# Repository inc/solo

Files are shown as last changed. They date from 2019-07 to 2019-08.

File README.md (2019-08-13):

# SOLO IOT motor controller

## Overview

SOLO is an IOT motor controller board designed by Lone Dynamics.

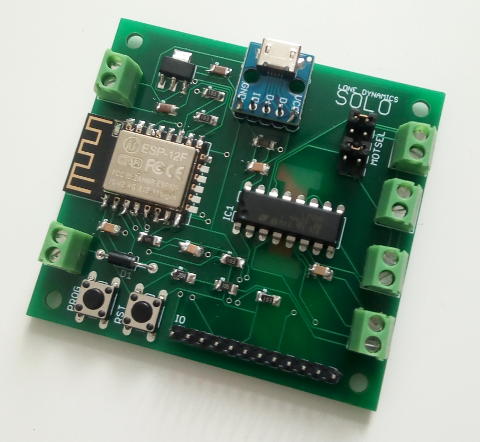
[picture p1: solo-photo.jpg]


## Features

  * Supports ESPEasy to provide a web-based interface and MQTT support over WiFi
  * Controls 2 (bidirectional) or 4 (unidirectional) DC motors
  * Power via MicroUSB or batteries and a solar panel
  * Battery voltage monitoring
  * Hand-solderable with a soldering iron

## Specifications

| | |
| --- | --- |
| Dimensions | 65mm x 60mm |
| WiFi Module | ESP-12E or F |
| Motor Controller | L293D |
| Power | MicroUSB, 4xAA NiMH batteries, 6V solar panel |

## Header Pinout

| Pin | Function |
| --- | --- |
| 1 | VCCBAT |
| 2 | VCC3V3 |
| 3 | ESPTXD |
| 4 | ESPRXD |
| 5 | ESPRST |
| 6 | GND |
| 7 | MOTOR12EN |
| 8 | MOTOR34EN |
| 9 | MOTOR1A |
| 10 | MOTOR2A |
| 11 | MOTOR3A |
| 12 | MOTOR4A |

## Board

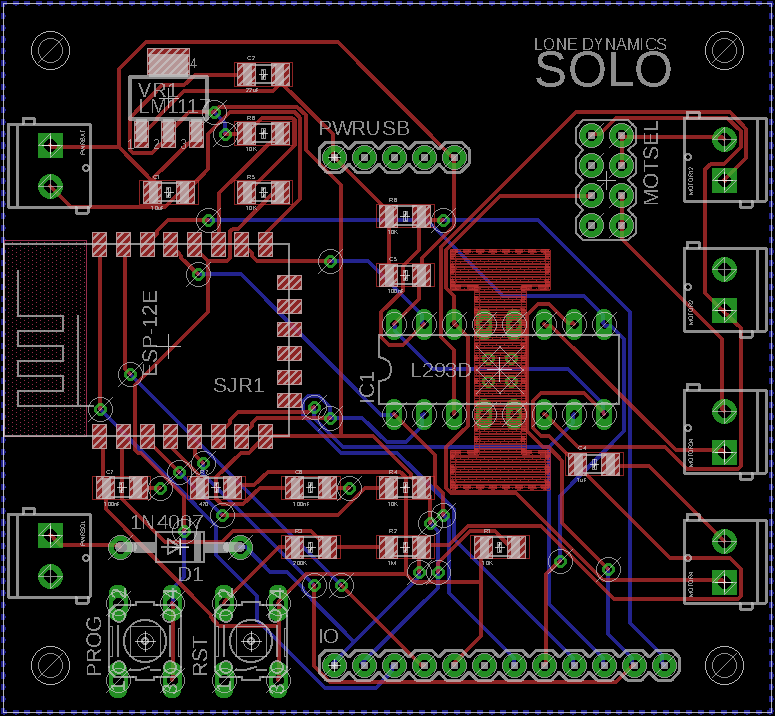
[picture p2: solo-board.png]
Board


## Schematics

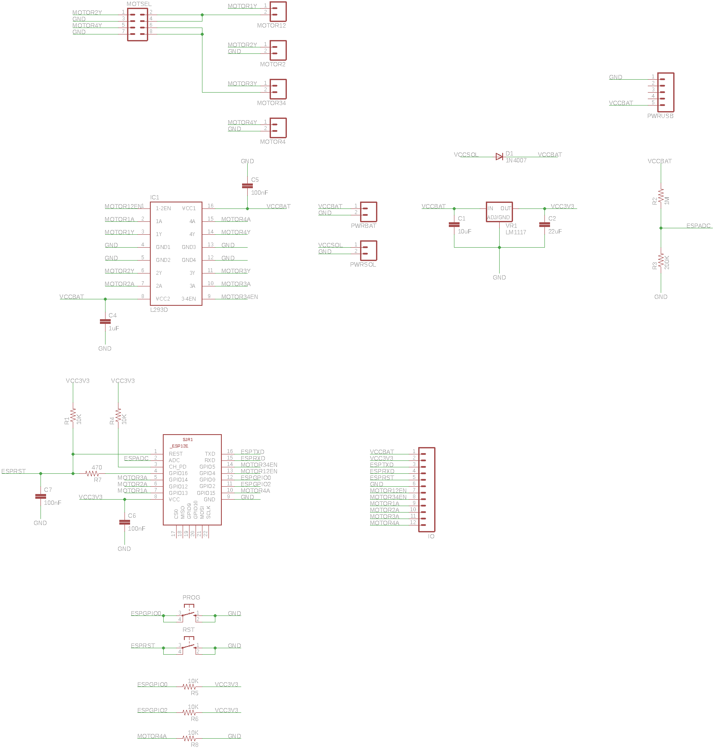
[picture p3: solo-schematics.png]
Schematics


## Known Issues (revision 0)

  * Pull-down resistors (10K) should be added to MOTOR12EN and MOTOR34EN to prevent the L293D from being enabled while the ESP is in sleep mode
  * Heatsink cutout doesn't expose copper
  * Has no built-in battery over-voltage protection

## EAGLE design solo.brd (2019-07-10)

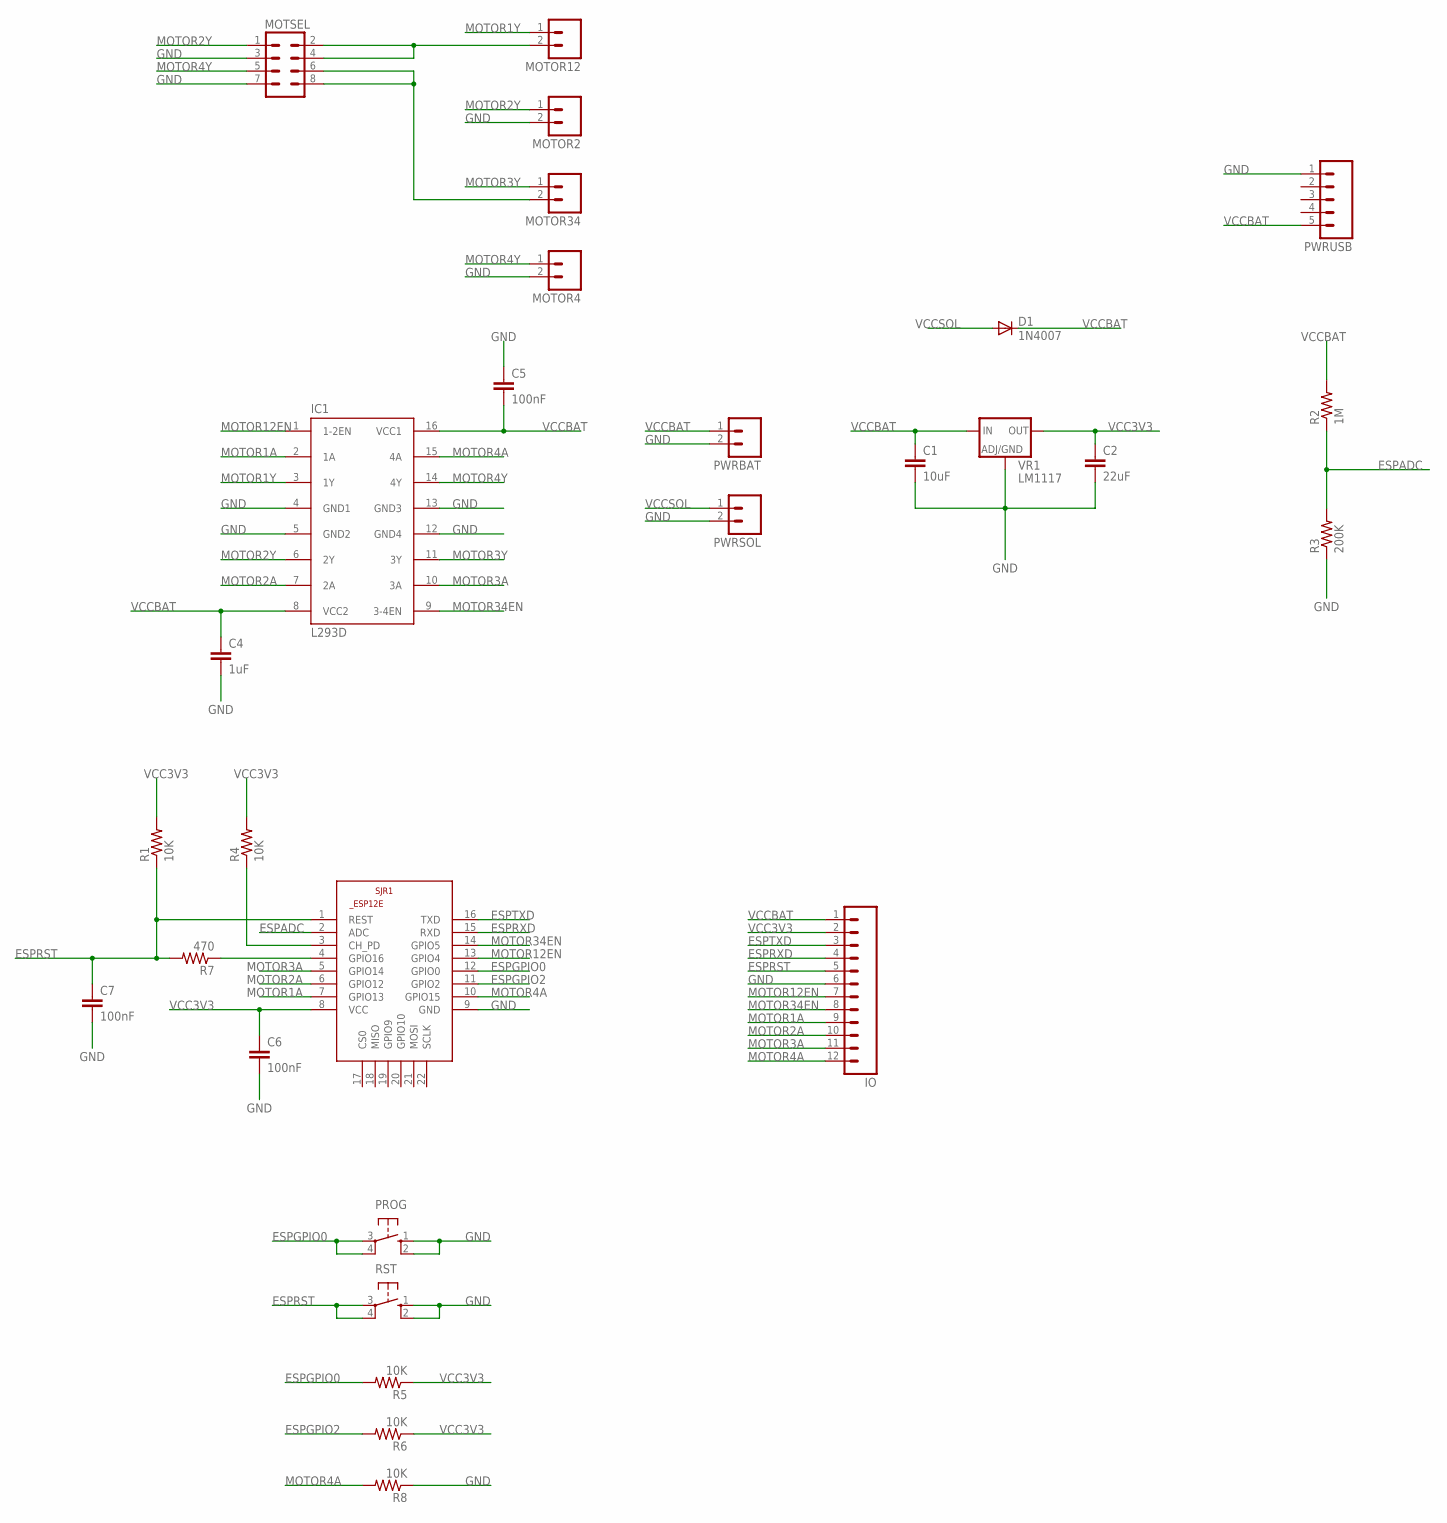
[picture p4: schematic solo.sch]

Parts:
C1: 10uF; 1206
C2: 22uF; 1206
C4: 1uF; 1206
C5, C6, C7: 100nF; 1206
D1: 1N4007; DO41-10
IC1: L293D; DIL16
IO: M12PTH; 1X12
MOTOR2, MOTOR4, MOTOR12, MOTOR34: M023.5MM; SCREWTERMINAL-3.5MM-2
MOTSEL: M04X2; 2X4
PROG: 10-XX; B3F-10XX
PWRBAT: M023.5MM; SCREWTERMINAL-3.5MM-2
PWRSOL: M023.5MM; SCREWTERMINAL-3.5MM-2
PWRUSB: M05PTH; 1X05
R1, R4, R5, R6, R8: 10K; 1206
R2: 1M; 1206
R3: 200K; 1206
R7: 470; 1206
RST: 10-XX; B3F-10XX
SJR1: ESP8266-12EESP12E; ESP8266-ESP12E
VR1: LM1117; SOT223

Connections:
ESPADC: R2.1, R3.2, SJR1.2 (ADC)
ESPCHPD: R4.1, SJR1.3 (CH_PD)
ESPGPIO0: PROG.3, PROG.4 (P1), R5.2, SJR1.12 (GPIO0)
ESPGPIO2: R6.2, SJR1.11 (GPIO2)
ESPRST: C7.1, IO.5, R1.1, R7.2, RST.3, RST.4 (P1), SJR1.1 (REST)
ESPRXD: IO.4, SJR1.15 (RXD)
ESPTXD: IO.3, SJR1.16 (TXD)
GND: C1.2, C2.2, C4.2, C5.1, C6.2, C7.2, IC1.4 (GND1), IC1.5 (GND2), IC1.12 (GND4), IC1.13 (GND3), IO.6, MOTOR2.2, MOTOR4.2, MOTSEL.3, MOTSEL.7, PROG.1 (S), PROG.2 (S1), PWRBAT.2, PWRSOL.2, PWRUSB.1, R3.1, R8.1, RST.1 (S), RST.2 (S1), SJR1.9 (GND), VR1.1 (ADJ/GND)
MOTOR1A: IC1.2 (1A), IO.9, SJR1.7 (GPIO13)
MOTOR1Y: IC1.3 (1Y), MOTOR12.1
MOTOR2A: IC1.7 (2A), IO.10, SJR1.6 (GPIO12)
MOTOR2Y: IC1.6 (2Y), MOTOR2.1, MOTSEL.1
MOTOR3A: IC1.10 (3A), IO.11, SJR1.5 (GPIO14)
MOTOR3Y: IC1.11 (3Y), MOTOR34.1
MOTOR4A: IC1.15 (4A), IO.12, R8.2, SJR1.10 (GPIO15)
MOTOR4Y: IC1.14 (4Y), MOTOR4.1, MOTSEL.5
MOTOR12EN: IC1.1 (1-2EN), IO.7, SJR1.13 (GPIO4)
MOTOR34EN: IC1.9 (3-4EN), IO.8, SJR1.14 (GPIO5)
unnamed: MOTOR12.2, MOTSEL.2, MOTSEL.4
unnamed: MOTOR34.2, MOTSEL.6, MOTSEL.8
unnamed: R7.1, SJR1.4 (GPIO16)
VCC3V3: C2.1, C6.1, IO.2, R1.2, R4.2, R5.1, R6.1, SJR1.8 (VCC), VR1.2 (OUT)
VCCBAT: C1.1, C4.1, C5.2, D1.C, IC1.8 (VCC2), IC1.16 (VCC1), IO.1, PWRBAT.1, PWRUSB.5, R2.2, VR1.3 (IN)
VCCSOL: D1.A, PWRSOL.1

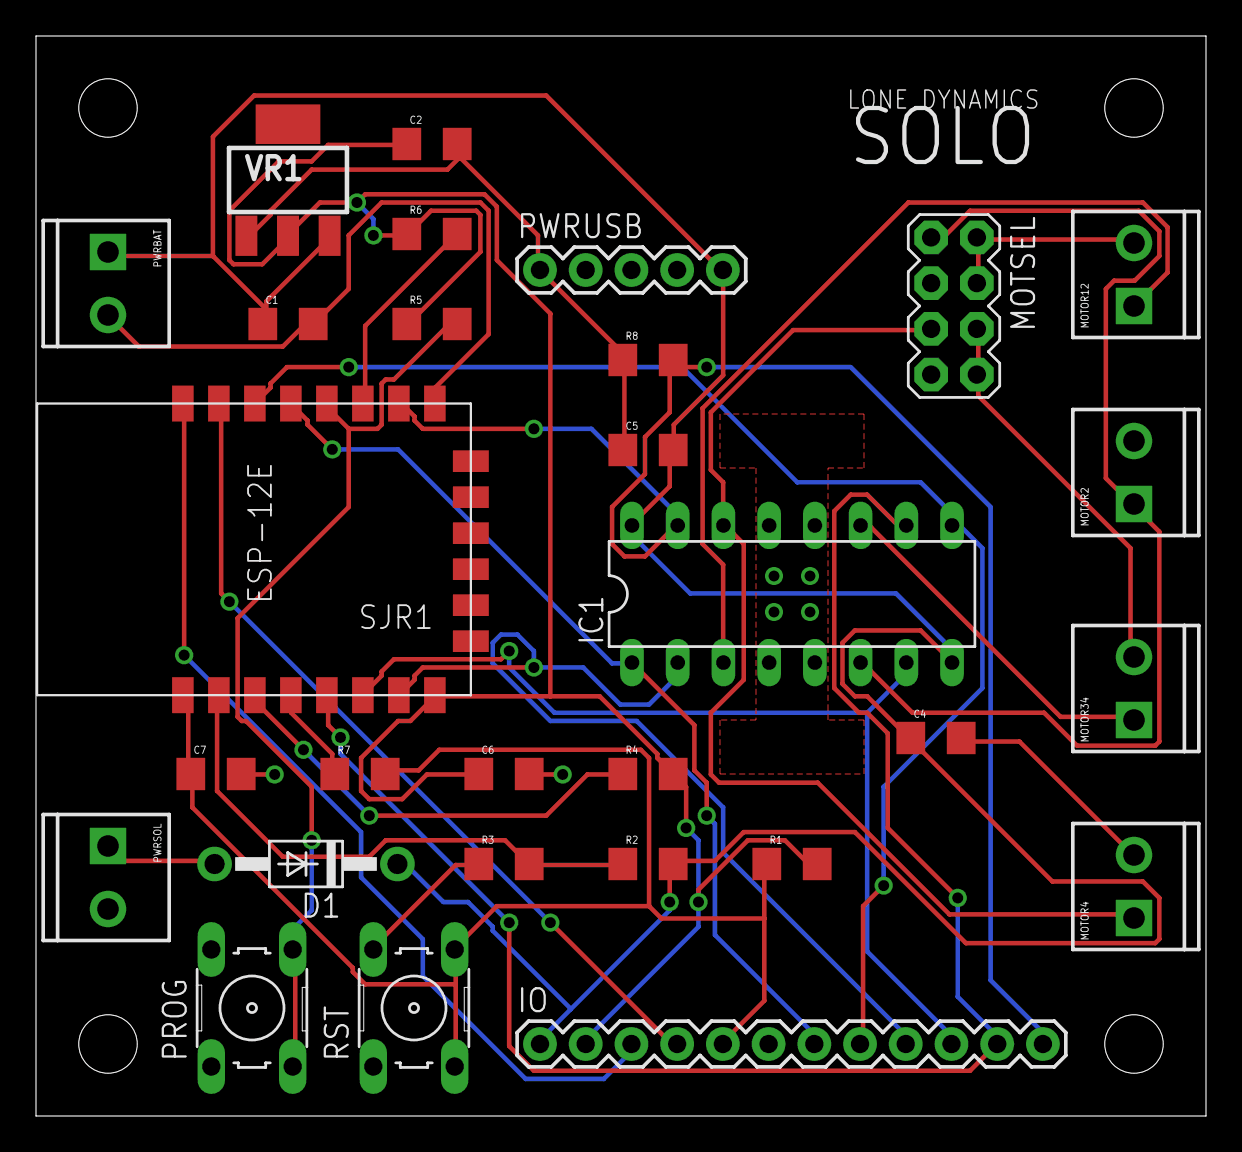
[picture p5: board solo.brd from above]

Board: 2 copper layers, 65.0 x 60.0 mm, 29 parts (0 on the bottom side), 24 nets.

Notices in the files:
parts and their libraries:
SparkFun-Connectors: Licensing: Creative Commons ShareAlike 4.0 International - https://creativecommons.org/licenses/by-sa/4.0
